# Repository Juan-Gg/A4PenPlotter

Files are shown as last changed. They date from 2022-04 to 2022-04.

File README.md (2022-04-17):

# A4PenPlotter
A4 Pen Plotter

This is a pen plotter capable of printing on A4 paper sheets. It is intended to be similar to the Aritma Amagraph pen plotter, be as compact and robust as posible as well as reliable.
It is controlled by means of an arduino with a grbl shield, wich drives the x and y motors, and the solenoid used for lifting-lowering the pen in response to g-code generated in inkscape and sent through grbl controller. Scroll down for a gif of it working, bill of materials, instructions...

Whatch a video here: https://www.youtube.com/watch?v=bf3e0SFeA1A
https://youtu.be/e5mVlJlMX_E
More projects here: https://juangg-projects.blogspot.ca/

(This is also on Thingiverse: https://www.thingiverse.com/thing:2504587, here as a backup)

Materials
1) 3d printed parts (All files starting with "Print"):
Print one of each (ending in x1) or two (ending in x2). One needs to be mirrored as specified in its name.

2) Non 3d printed parts:
a)Metal profiles:
Stls included for dimensions. Material specified in their name.
In addition, two 6mm ID 30 mm long 0,5 mm thickness brass tubes are needed to act as
bearings between x carriage and the steel shafts.

b)Screws (and their nuts):
1 M4x20 mm
1 M4x40 mm
15 M3x12 mm
4 M3x30 mm
10 M2,5x8mm
8 2x10 wood screws
2 M4 wing nuts (optional)

c)Electronics:
1 Arduino UNO
1 arduino CNC shield (with drivers)
Mosfet circuit to drive the solenoid using the spindle pin(example included)
1 Enstop
1Power switch
1 Jack conector
1Red LED
1 470 Ohm resistor
Asorted wires
USB cable
A computer to generate and send the g-code to the plotter.

d) Actuators:
2 NEMA 17 x 35 mm stepper motors.
1 Spring loaded 12v solenoid (mine was from an old printer, use the one you have and glue
it in place.

e) Misc:
Paper rollers from an old printer (you can print them yourself)
Sand paper to glue on the 12mm alumninum tube to grip the paper
4 Ball bearings 4mmID 13mmOD 5mm thickness
Heatsrink tubing
Cable ties
6mm wide Belt and pulley
6 x 12 mm spring

And the compulsory one: Some free time.

Instructions
1) Mechanical assembly:
Follow the photographs, drawings, and the assembly reference step file, it should be pretty obvious where everything goes.
Some hints:

Captive nuts that hold everything toguether are located on the inside of the holes where the profiles go (there is an hexagonal slot in which they fit), insert them and engage the screw BEFORE putting the profile in.

The 12 mm OD aluminum tube is fixed to the motor shaft in one end and to an M4 screw on the other end by means of three M 2.5 x 8 mm screws in a triangle arrangement (see photo gallery), with the nuts inside, so they press on the shaft. This allows to center it precisely. If you find it too complicated, you can always use lots of tape, but that its not very professional, neither reliable.

X motor screw holes are a bit enlarged to adjust belt tension.

There is one spring in the moving carriage that presses the pen against tha paper. This spring is kept in place between two small circular slots. The solenoid spring must overcome this spring force in order to push the lever up.

Sandpaper is wraped in a spiral way around the 12 mm OD tube in order to grip the paper. You can glue this with contact glue or similar.
Don't hesitate to ask any questions, and sorry for not providing step-by-step guide with photographs. I am not able to do that at the moment.

2) Electrical assembly
I assume I don't have to provide an schematic for the main power switch and LED.

The tricky part is the solenoid driving circuit. While you can use the schematic provided with a P-chanel MOSFET, I encourage you to use an N-chanel MOSFET so you can get rid of the transistor. Look for schematics online.

I added an LED to check whether the solenoid is powered or not and some buttons (Pause, continue, reset, e-stop) These are not necesary for it to work, but they come in handy.
3) Loading and configuring grbl
Download grbl here: https://github.com/grbl/grbl
Configuration instructions: https://github.com/gnea/grbl/wiki/Grbl-v1.1-Configuration
Scroll down for the settings I used. (Steps per mm may vary in your machine, just print some squares and keep adjusting until you get it right)

4.1) G-code generation (Vector files)
Use this for lineal drawings, or with dxf, svg...files.

You can convert bitmaps to vector on inkscape on path > trace bitmap.

To generate g-code, I used inkscape and jtech photonics laser tool (https://jtechphotonics.com/?page_id=2012).

This plug in needs some modifications in order to work for our needs:

Go to C:\Program Files (x86)\Inkscape\share\extensions\laser.py, open it with your
favourite text edditor (I used notepad ++) and make sure the following three lines look like
in the photo below:

This will allow us to use custom g-code to turn the laser(in our case the solenoid) on and off.
Otherwise it will add laser power and more stuff. This way it worked for me.
I used the spindle enable pin on the cnc shield (m8 on, pen down, m9 off, pen up), but you can use the coolant pin as well.

4.2) G-code generation (Bitmaps)
Use this to print images like the submarine photo you can see above. Keep in mid that this will take much longer, depending on the resolution used.

For this, I used another plug-in for inkscape:
https://github.com/305engineering/Inkscape
This needs no modifications.
5) G-code sending
I used grbl controller (https://github.com/zapmaker/GrblHoming/releases)
This program will also let you configure grbl once it is loaded.

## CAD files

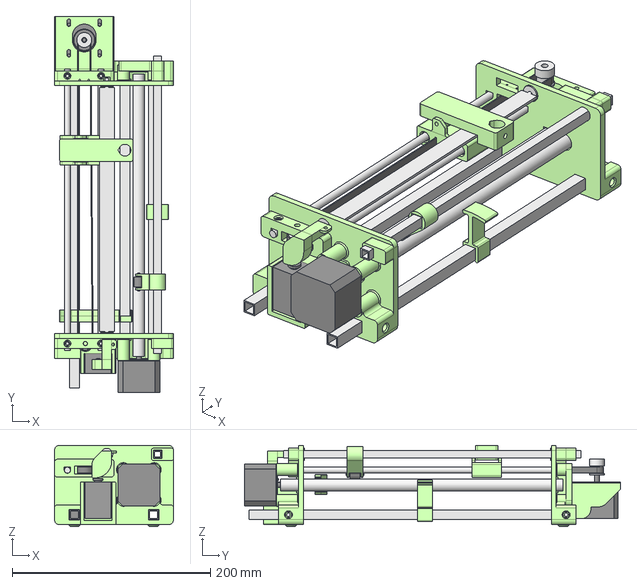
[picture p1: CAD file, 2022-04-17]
STL and STEP files/Assembly_reference.step
120.0 x 379.5 x 82.0 mm

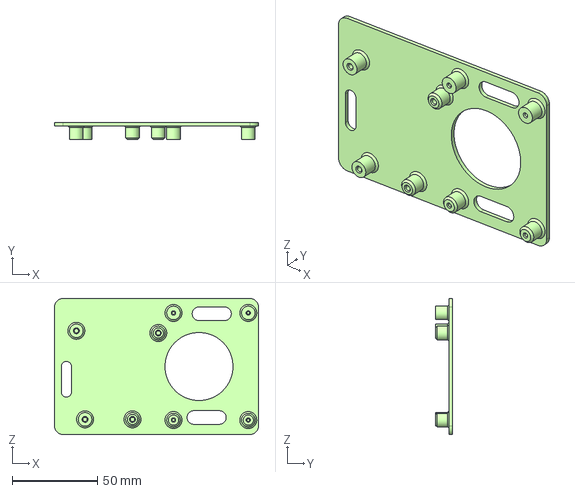
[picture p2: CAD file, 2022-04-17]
STL and STEP files/step_electronics_support_2.step
120.0 x 10.0 x 80.0 mm

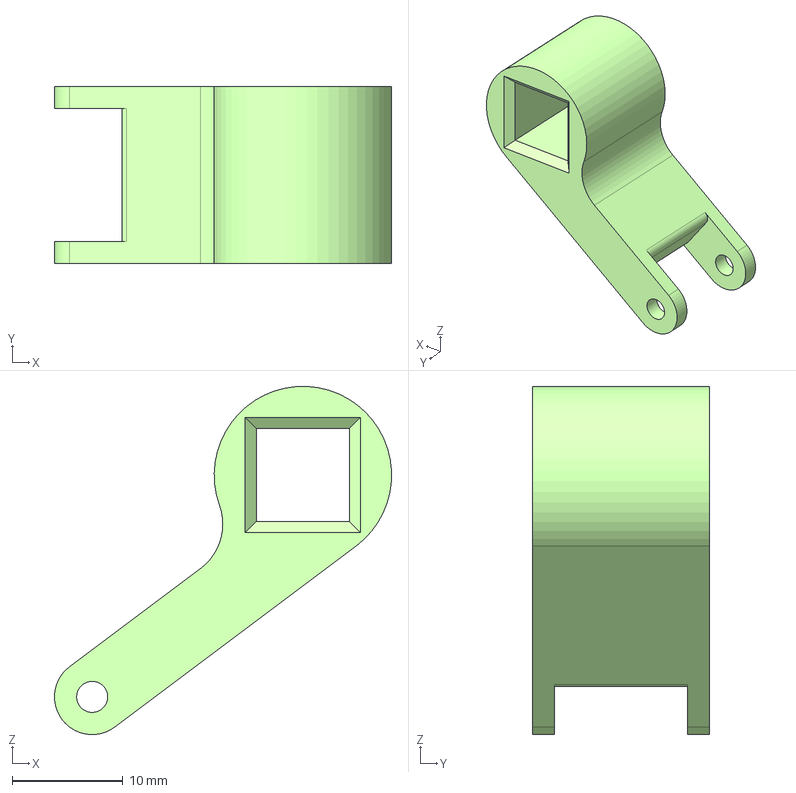
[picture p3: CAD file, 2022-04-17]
STL and STEP files/step_Paper_roller_support.step
30.4 x 16.0 x 31.4 mm

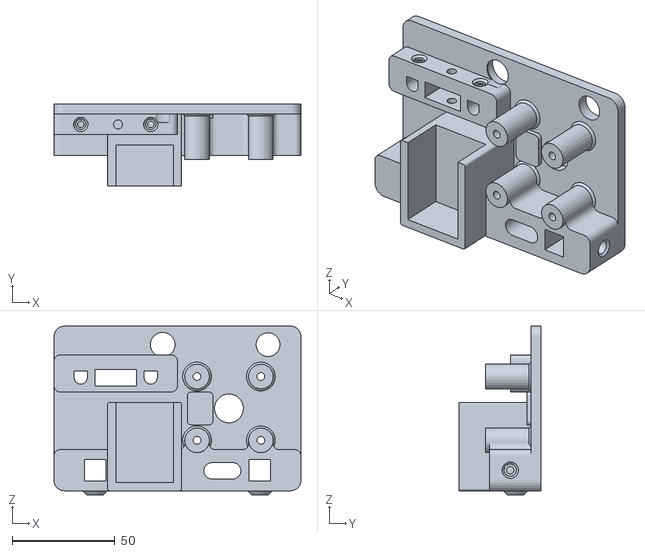
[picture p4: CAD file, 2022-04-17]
STL and STEP files/Print_Right_Frame_x1 (1).stl
120.0 x 40.0 x 82.0

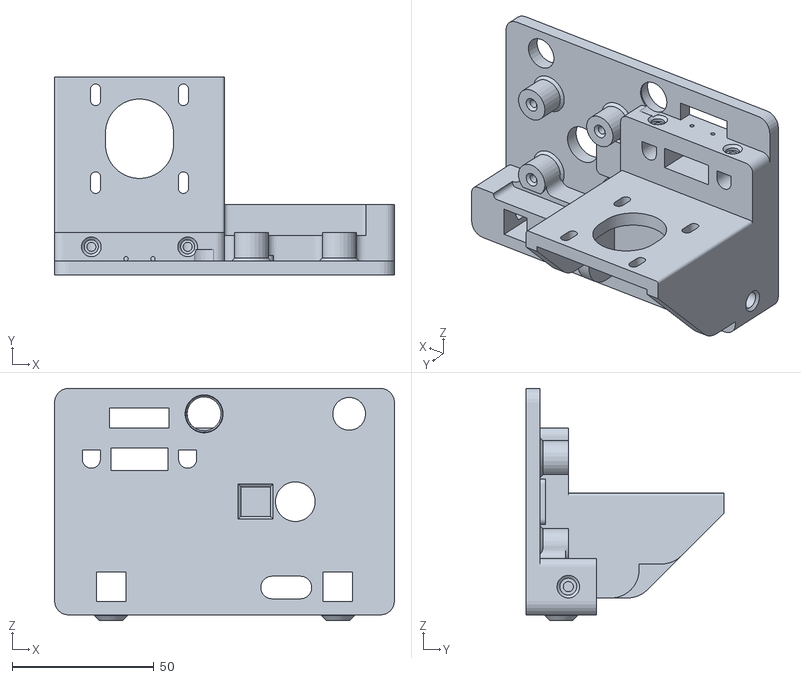
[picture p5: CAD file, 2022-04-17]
STL and STEP files/Print_Left_Frame_x1.stl
120.0 x 70.0 x 82.0

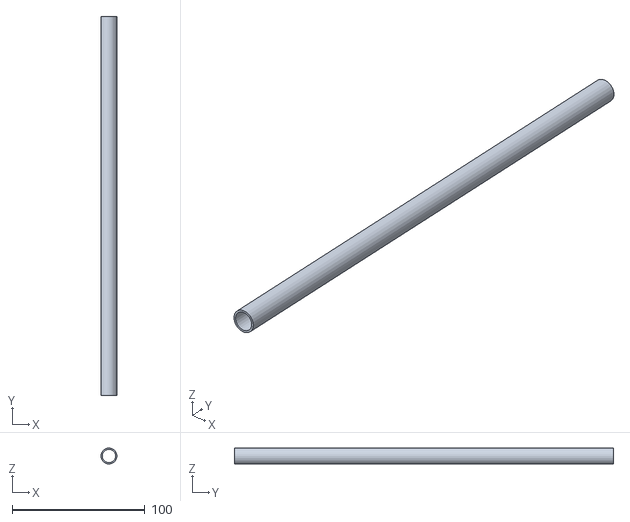
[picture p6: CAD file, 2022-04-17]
STL and STEP files/Alu_Round_Profile_12_mm.stl
12.0 x 285.0 x 12.0

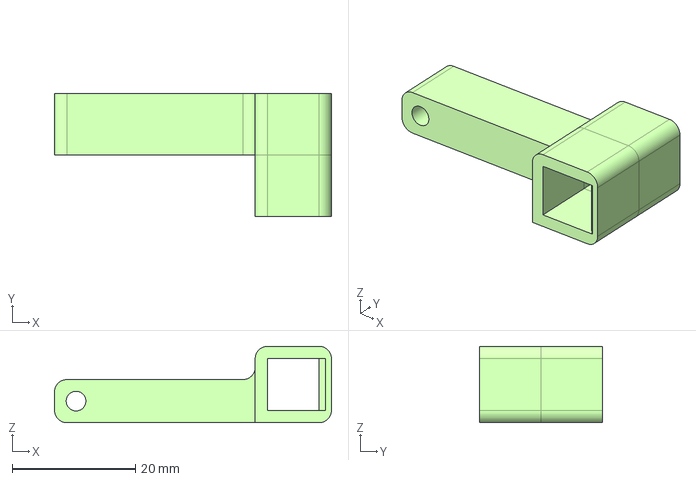
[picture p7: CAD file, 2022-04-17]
STL and STEP files/step_Paper_roller_lever1.step
45.0 x 20.0 x 12.4 mm

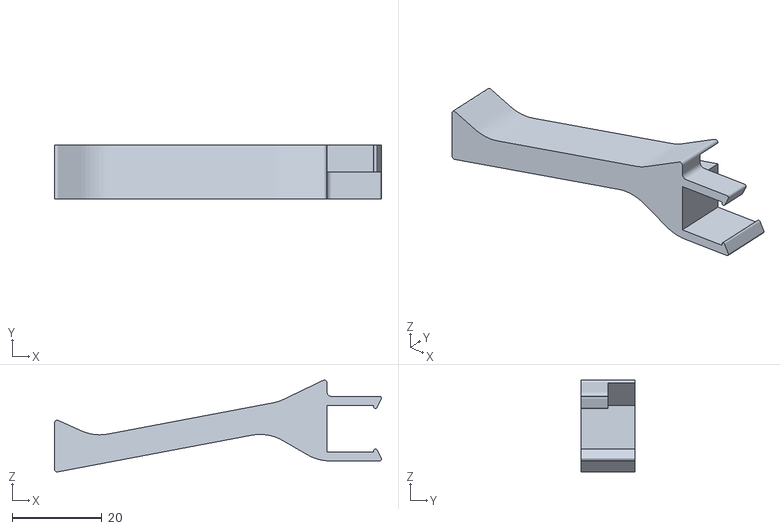
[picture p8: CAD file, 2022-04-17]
STL and STEP files/Print_Paper_guide_b_x2_one_mirrored.stl
73.0 x 12.0 x 20.5

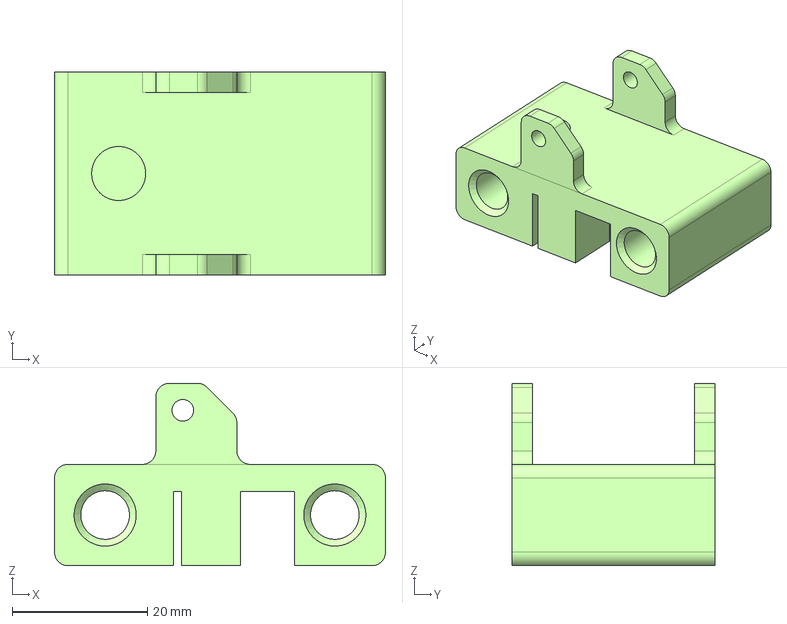
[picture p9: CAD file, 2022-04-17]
STL and STEP files/step_X_carriage.step
49.0 x 30.0 x 27.0 mm

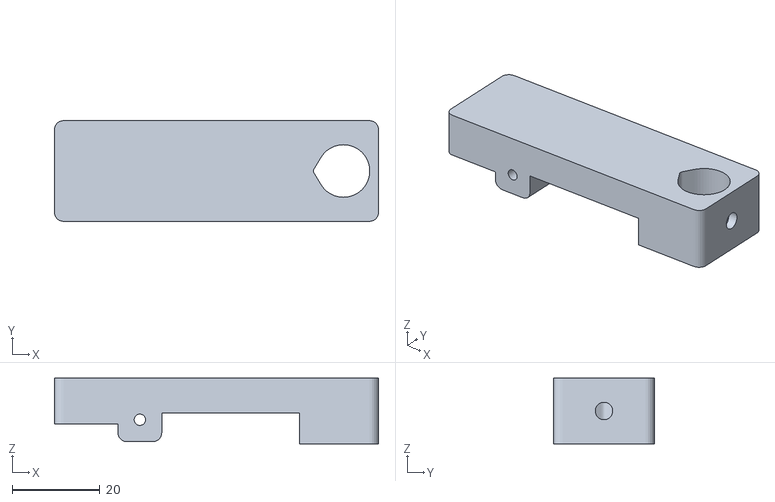
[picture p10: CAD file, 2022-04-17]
STL and STEP files/Print_Pen_lever_x1_.stl
74.0 x 23.0 x 15.0

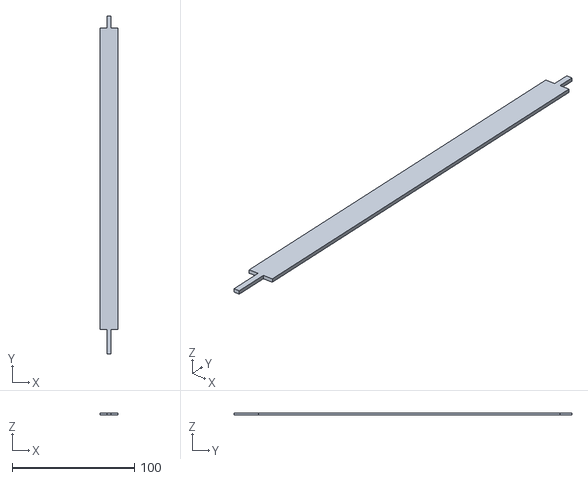
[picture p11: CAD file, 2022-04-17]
STL and STEP files/Alu_15x2_mm_profile.stl
15.0 x 276.0 x 2.00

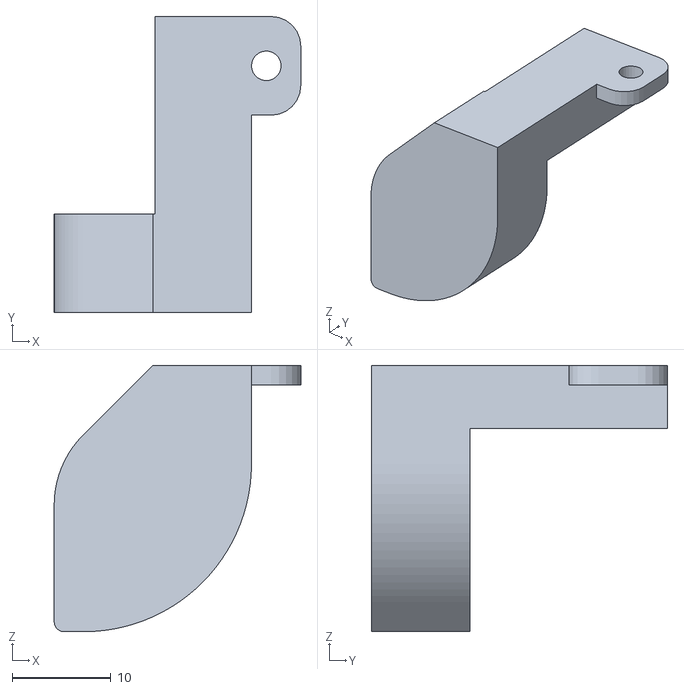
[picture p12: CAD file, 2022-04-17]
STL and STEP files/Print_Up-down_lever_x1.stl
25.0 x 30.0 x 27.0

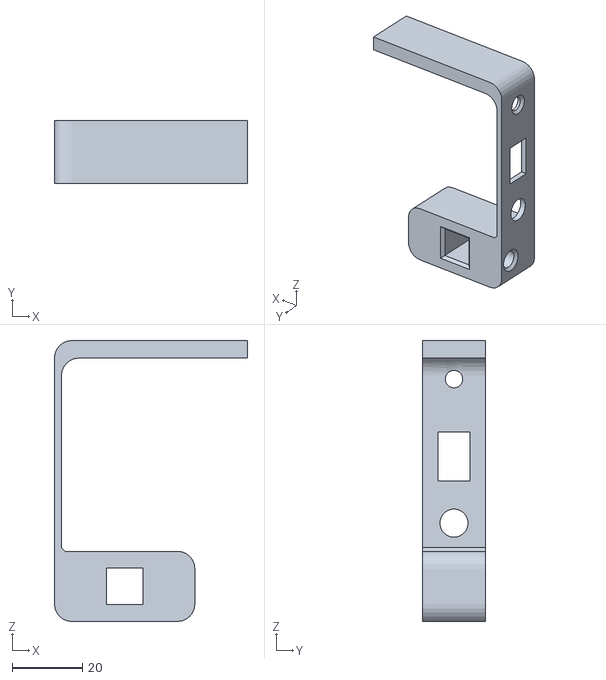
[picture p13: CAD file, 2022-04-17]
STL and STEP files/Print_Switch_support_plate_x1.stl
55.0 x 18.0 x 80.0

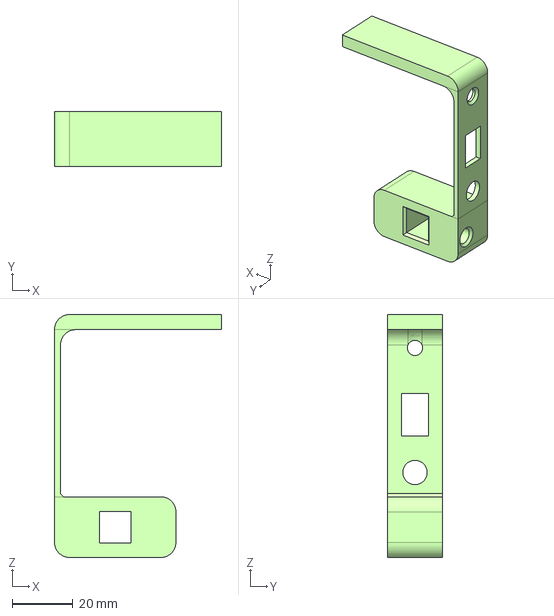
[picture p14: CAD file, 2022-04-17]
STL and STEP files/step_electronics_support_1.step
55.0 x 18.0 x 80.0 mm

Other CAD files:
STL and STEP files/Print_Electronics_support_plate_x1.stl
STL and STEP files/Print_Papper_roller_support_x2.stl
STL and STEP files/step_Y_bearing_support.step
STL and STEP files/Print_Papper_roller_lever_x1.stl
STL and STEP files/Alu_square_profile_10_mm.stl
STL and STEP files/Alu_square_profile_10_mm_b.stl
STL and STEP files/Alu_square_profile_8_mm.stl
STL and STEP files/Bearing_13x4x5_x4mm.stl
STL and STEP files/Print_Left_Frame_Y_bearing_support_x1.stl
STL and STEP files/Print_Papper_roller_end_lever_x1.stl
STL and STEP files/Print_X_axis_carriage.stl
STL and STEP files/Steel_shaft_6mm.stl
STL and STEP files/step_Left_Frame.step
STL and STEP files/step_Pen_support.step
STL and STEP files/step_Right_Frame.step
STL and STEP files/step_paper_guide_1_mirror_.step
STL and STEP files/step_paper_guide_2_x2.step
STL and STEP files/step_paper_roller_lever_2.step
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
